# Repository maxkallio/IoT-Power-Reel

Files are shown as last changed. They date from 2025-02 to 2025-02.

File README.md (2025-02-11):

## Introduction

`IoT - Power` is a system for lending power reels in the HBO-ICT faculty on campus.

Students can use this system with their student cards to authenticate to the server, so that they can retrieve a power reel.

## Development

This project consists of two major components, found in their respective directories.

- Embedded
- Web

These two components work together to form the system as a whole.

### Embedded

The embedded directory contains all code for the microcontroller. IoT - Power uses <a href="https://platformio.org/">PlatformIO</a>, a framework for embedded systems for embedded code.

### Web

The web component consits of a database (SQL, MariaDB) and a LEMP stack.

### Running IoT - Power

Both components have to be deployed for this project to work.

#### Web
```shell
docker-compose -f docker-compose-test.yml up -d --force-recreate --build
```

#### Embedded

For the embedded system you first need to change the config to point to the deployed webserver. Then use PlatformIO to compile and upload the code to your microcontroller.
There's two different deployment modes. For each deployment mode different firmware is built. With platformIO you can choose between:
- Offline mode
- Online mode

Refer to the platformio.ini to find the differences between the two. There's some additional configuration needed for each mode however.

##### Online mode

In the platformio.ini you need to change the `BASE_URL` param to the IP address of the backend server.

e.g. `\"http://145.92.189.162/api/\"`. Please note the escape backticks in this `BASE_URL` param, this is mandatory!

##### Offline mode

In `/embedded/src/locker-offline.cpp` the inititlization of a struct `locker` named `lockers` can be found. This struct is a mapping of locking pins to the lockers along it's current state. In it's header file you can find it's definition.

You need to change `lockers` to the amount of lockers used in the deployment, with a correct mapping of locking pins to the locker.# IoT-Power-Reel
# IoT-Power-Reel
# IoT-Power-Reel

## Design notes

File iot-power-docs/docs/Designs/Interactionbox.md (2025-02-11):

# Interaction Box Design

## The board

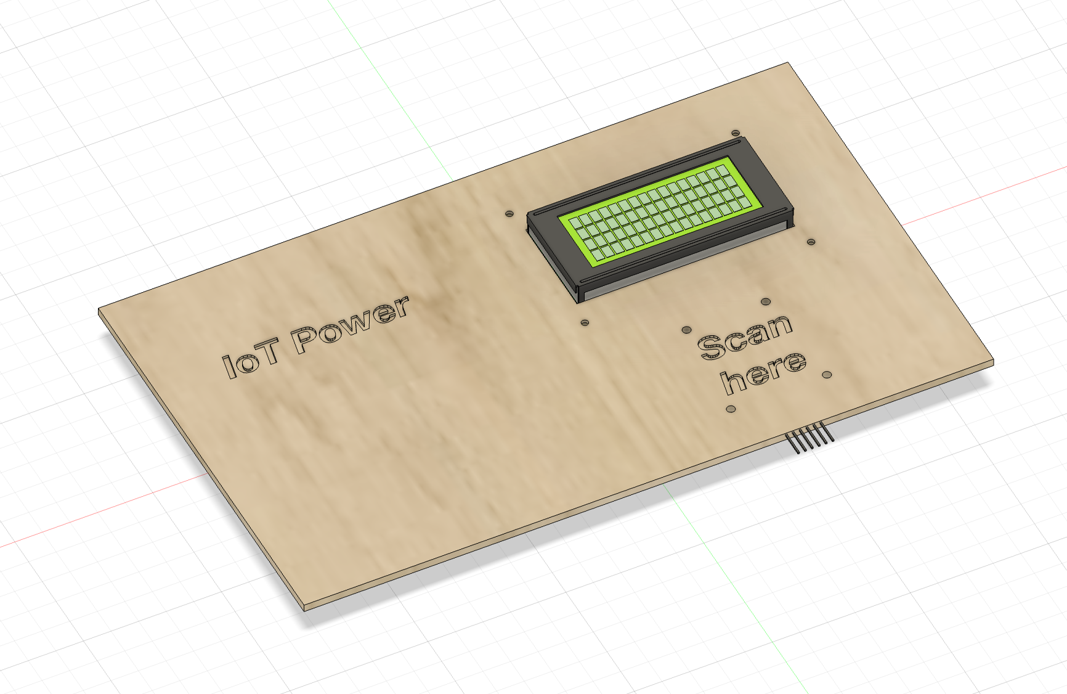
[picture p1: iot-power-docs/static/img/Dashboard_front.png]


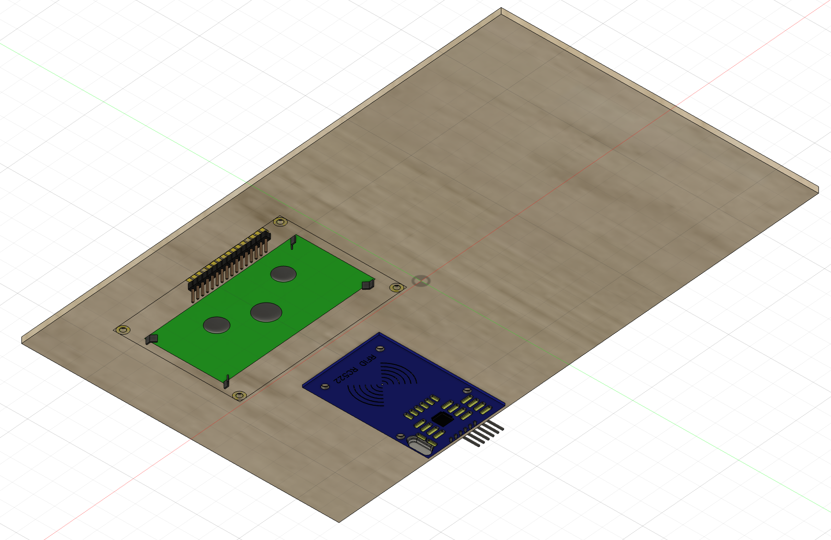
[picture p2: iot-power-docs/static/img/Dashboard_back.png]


### Overview
This is a main board to hold essential components for the device. It is crafted to  mount a 16x4 LCD screen and an RC522 RFID scanner module. The board will be fabricated using a laser cutter and 3mm plywood.

"IoT Power" is engraved on the left side of the board and "Scan here" is engraved near the RFID scanner to indicate its purpose.

### Material specifications
- 3mm plywood  
- The board dimensions are 250mm x 150mm

### Notes
- The engraved labels will guide users to understand the functionality of each component.
- The plywood material gives an eco-friendly aesthetic, while being sturdy enough to hold the components securely.

### Files

- [Fusion 360 file](https://gitlab.fdmci.hva.nl/IoT/2024-2025-semester-1/group-project/yoogaaciinuu24/-/blob/main/design/Dashboard.f3z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)
- [STL file (preview on GitLab available)](https://gitlab.fdmci.hva.nl/IoT/2024-2025-semester-1/group-project/yoogaaciinuu24/-/blob/main/design/Dashboard.stl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)
- [DXF file for laser cutting](https://gitlab.fdmci.hva.nl/IoT/2024-2025-semester-1/group-project/yoogaaciinuu24/-/blob/main/design/Dashboard_with_engraving.dxf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)

### Update

This board was updated and transformed into a box to hold more embedded components such as the breadboard and the microcontroller

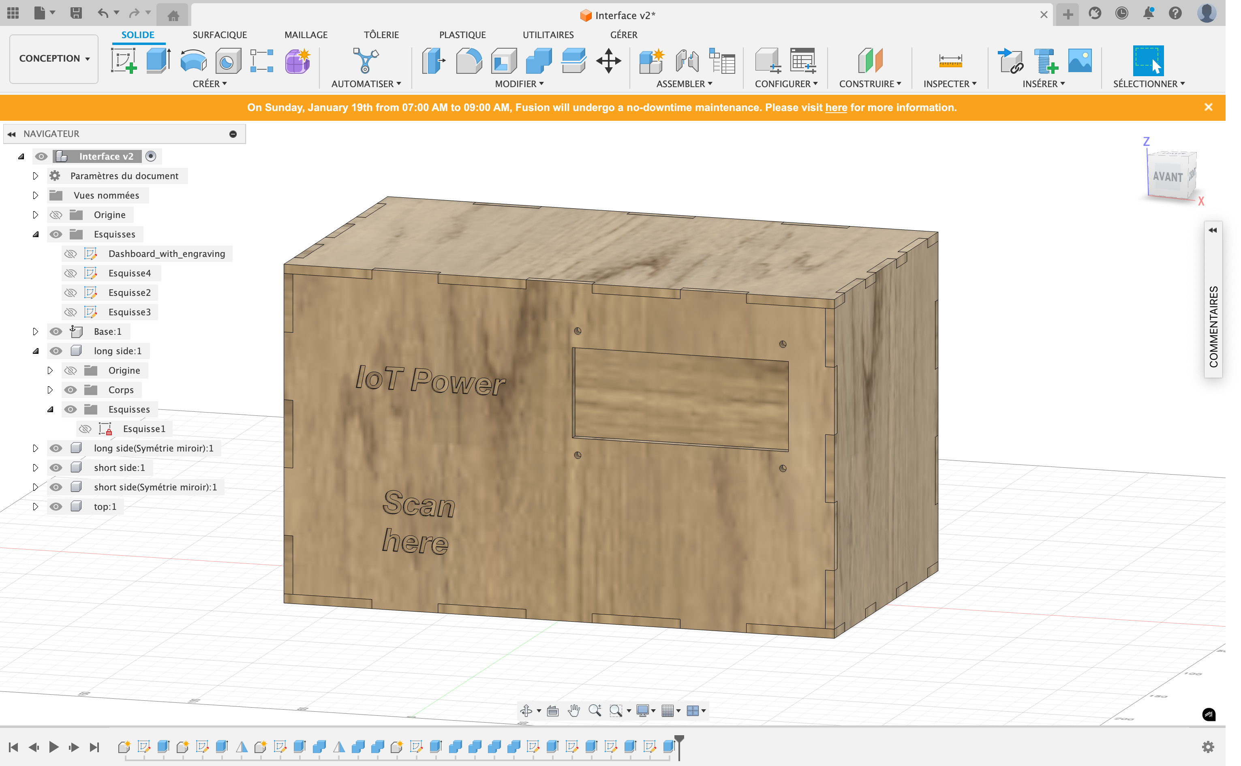
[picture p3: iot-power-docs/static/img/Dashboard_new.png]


## The locker

## Overview

The second version of the locker prototype improves upon the initial design by incorporating finger joints for increased durability and ease of assembly. This version also includes stackable features and additional support to align with the project's requirements for modularity and robustness.

---

## Key Features

- **Finger joints for durability**
   - Finger joints were designed in Fusion 360 to improve the structural integrity of the locker.
   - The joints allow precise interlocking of panels, reducing the reliance on adhesives.
   - A tutorial was followed to implement these joints effectively ([Fusion 360 Finger Joints Tutorial](https://www.youtube.com/watch?v=ZrcqauNvt0M)).

- **Two 4mm wood sheets**
   - The prototype uses 4mm-thick MDF wood sheets, chosen for their affordability and ease of laser cutting.
   - Edges are reinforced with finger joints to ensure durability under repeated stacking or handling.

- **Stackable edges**
   - The top and bottom edges of the locker were modified to include alignment guides, allowing multiple lockers to be securely stacked.
   - This feature adds modularity and flexibility for applications requiring expandable storage systems.

- **Adjustments with AutoCAD**
   - After initial design in Fusion 360, minor adjustments were made in AutoCAD adjust the dimensions.
   - The adjustments focused on tolerances to account for the laser cutter's kerf and material thickness.

---

## Manufacturing process

1. **Design**
   - Created the overall shape and added finger joints in Fusion 360.
   - Ensured all edges aligned perfectly for clean assembly.
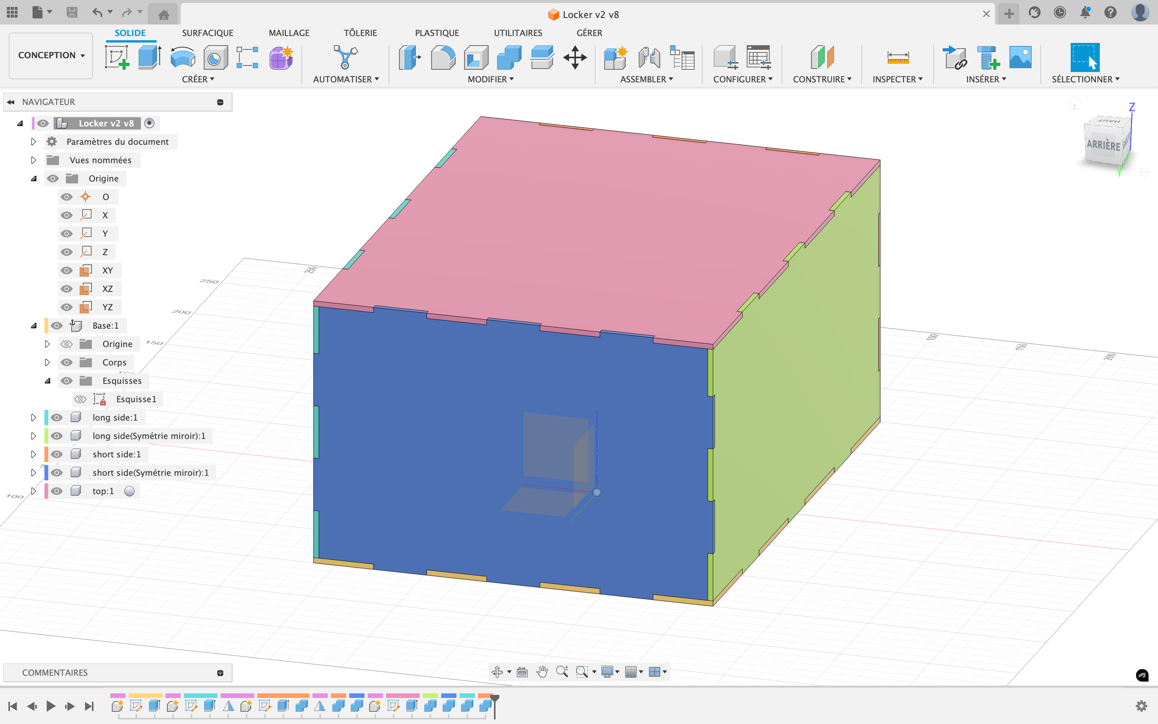
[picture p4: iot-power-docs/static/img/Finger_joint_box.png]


2. **Adjustment**
   - Exported the design to AutoCAD for precise dimensional adjustments.
   - Verified tolerances for the laser cutter.
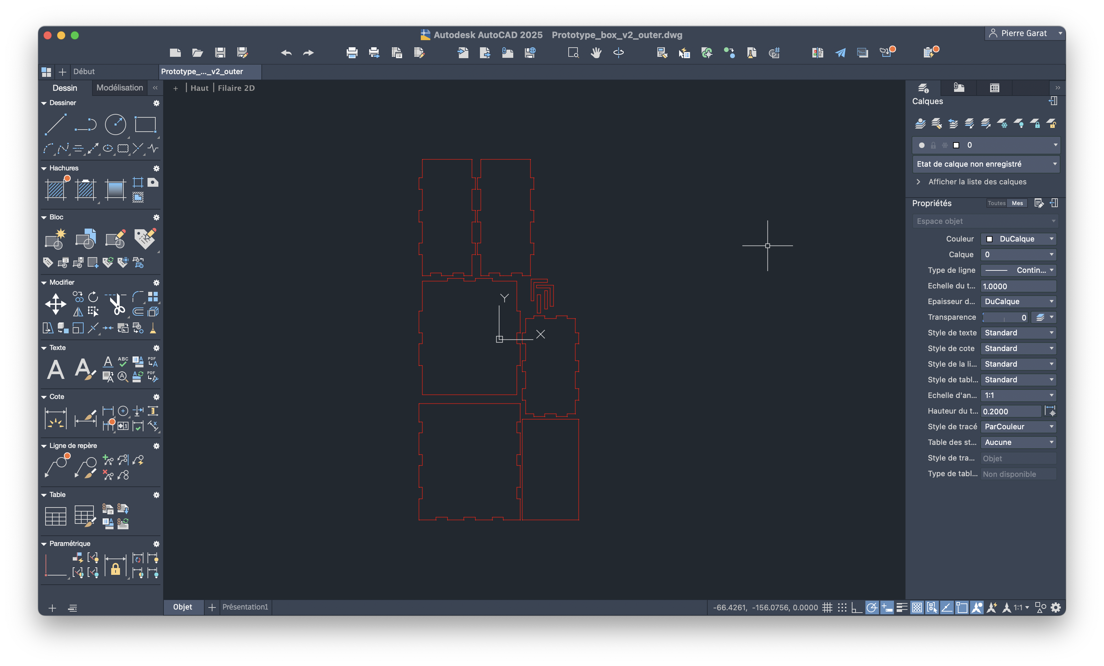
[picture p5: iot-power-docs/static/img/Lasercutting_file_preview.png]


3. **Fabrication**
   - Laser-cut all panels from two 4mm MDF sheets.
   - Assembled the panels manually, interlocking the finger joints.
   - Tested stacking alignment and structural integrity.

## Files

- [Fusion 360 file](https://gitlab.fdmci.hva.nl/IoT/2024-2025-semester-1/group-project/yoogaaciinuu24/-/blob/main/design/Locker_v2.f3d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)
- [STL file (preview on GitLab available)](https://gitlab.fdmci.hva.nl/IoT/2024-2025-semester-1/group-project/yoogaaciinuu24/-/blob/main/design/Locker_v2.dxf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)
- [DXF file for laser cutting](https://gitlab.fdmci.hva.nl/IoT/2024-2025-semester-1/group-project/yoogaaciinuu24/-/blob/main/design/Prototype_box_v2.dxf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)
- [DXF outer file for laser cutting](https://gitlab.fdmci.hva.nl/IoT/2024-2025-semester-1/group-project/yoogaaciinuu24/-/blob/main/design/Prototype_box_v2_outer.dxf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)

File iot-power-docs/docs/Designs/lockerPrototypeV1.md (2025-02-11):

# First prototype of the locker

The first prototype was created using Fusion 360. This tool makes it possible to create 3D designs that can be used in the makers lab. By exporting the sketch made in the tool the laser cutter can be used. To explain the way of making the design I have created this documentation file. After explaining the prototype I will discuss the improvements that have to made in the second prototype. The following topics will be discussed in this file.

1. The design
2. Laser cutting
3. The materials
4. Improvements for the next prototype

## The design

As mentioned before Fusion 360 was used in the design of the first prototype. Below is an image of the design with numbers of parts that are explained below. The Fusion 360 file is also added to the project in the static/design folder named LockerDesignV1.

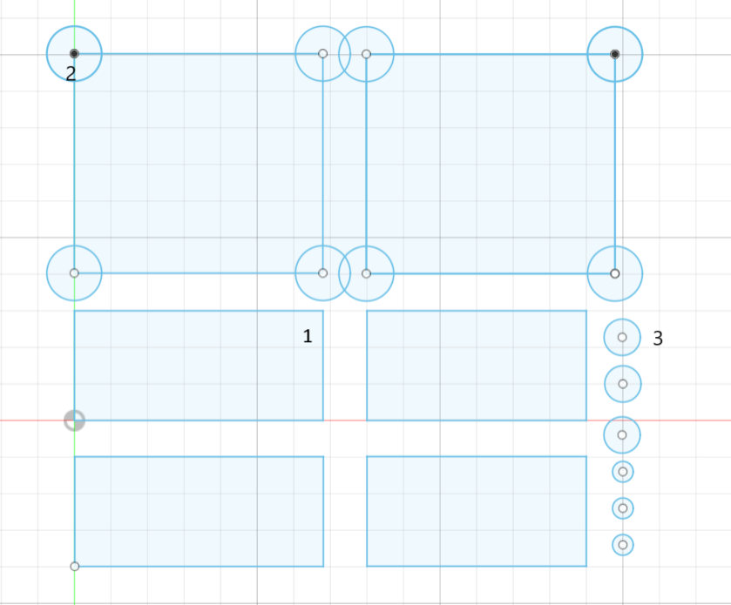
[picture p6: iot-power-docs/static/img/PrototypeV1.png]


1. These are the wall of the locker. There are two shorter back wall and two longer side walls. The dimensions used are based on power cable dimesnions found on the internet. I found multiple dimensions so to be sure the power cable would fit I used the biggest dimensions found.

2. These are the top and bottom parts of the locker. The cicles in the corners are used to make the indentations in the plywood. After uploading the sketch to the laser cutting program I removed the part of the circle that exceeds the boundaries of the rectangle. Only the ceeling of the locker should have a indentation but I used the indentation marks of the wall to make raised cutouts to attatch to the floor of the locker. This was done by moving the new quarter circles to the side of the box and cutting these out separately.

3. These circles are used to make the doorknob of the locker. By having multiple smaller and at least one bigger circle the circles can be glued together. This makes for a cone with a bigger end. This is turn results in a doorknob.

## Laser cutting

After making the design the next step of the prototype was using the laser cutter in the Makerslab. This was done by uploading the sketch to a USB and loading it into the computers used for laser cutting. I gave the lines that should be indented a red color and the lines that should be cut a black line. By setting different laser depts in the settings of the tool used by the computer I was able to make a differentiation in cutting and engraving. I baught the thickest plywood available and set the cutting settings accordingly. By weighing the plywood down at the edges I was able to compensate a slight curve in the wood.

After using the buttons on the laser cutter I found that the design of the locker was to big for the plywood. This resulted in me having to cut the desing in half and cutting two separate pieces of plywood. This was no big issue because I could use the design tool of the computer attatched to the laser cutter to do this. After cutting two pieces of plywood I now had the plywood parts to assamble the locker. I did not have all the materials yet because I needed bolts, nuts and a doorhinge. I taught that I could get these parts from the Makerslab but only the correct bolts were present. This resulted in me having to go to Praxis to get the right parts. The walls, ceeling and floor were glued together and the bolts were screwed into the wood using a screwdriver. By gluing the circels together I created the doorknob. I also glued the raised corners to the floor of the locker this was the last part to add.

After all these steps the locker was assembled. The images below shows the locker after it was finished.

### Locker top view
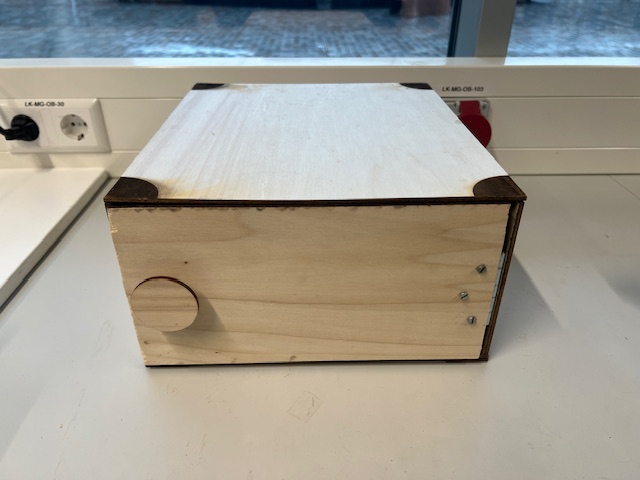
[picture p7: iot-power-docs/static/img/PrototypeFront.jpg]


### Locker top view with open door
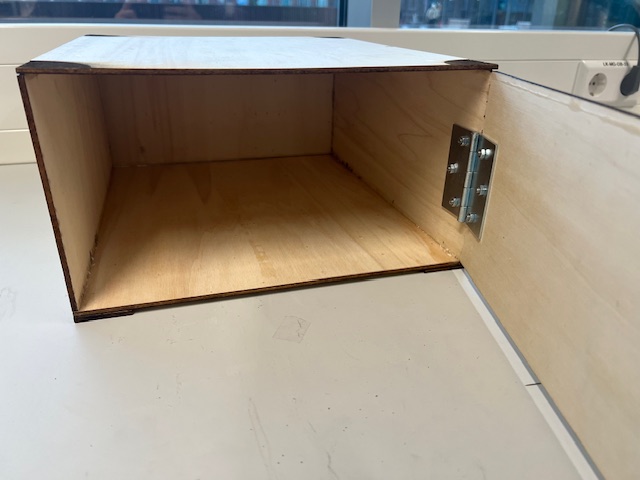
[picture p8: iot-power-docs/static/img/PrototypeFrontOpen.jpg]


### Locker bottom view
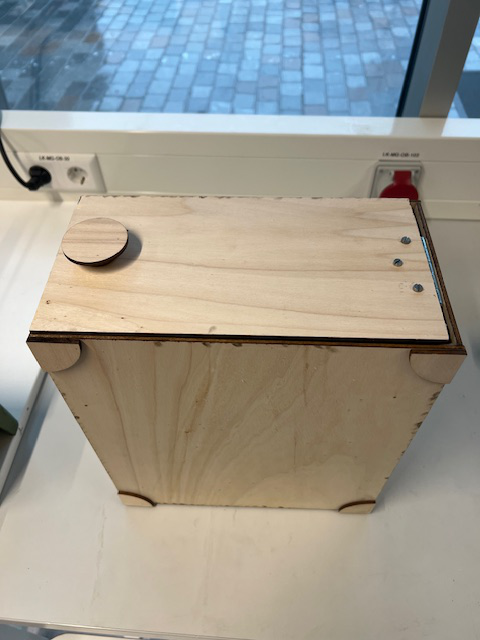
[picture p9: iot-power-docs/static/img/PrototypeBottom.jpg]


## The materials
There are multiple materials used for the locker. The most important part is the plywood used. we asked the Makerslab for the strongest wood they had and they advised me to use MDF wood. This plywood is still not very strong or thick but if we want to use stronger wood we have to decide on using wood baught from a hardware store.

As mentioned before the makerslab only had bolts that could be used in assembling the locker. The Makerslab had nuts but not the correct size for the hinge we were using. The hinge itself had to be baught from Praxis because the Makerslab nad no hinges available. 

The hinge baught was a 70x70mm doorhinge of the brand I-Fix. The nuts used have a size called M4 and are described as zeskantmour gegalviniseerd. The producer of the nuts is called Maxeda DIY. The bolts used for the locker were available in the makerslab and were the smallets bolts available. These were the only bolts to fit the holes in the doorhinges.

## Improvements for the next prototype
After building the prototype we found that the wood used in the desing was not very sturdy. The wood used should be altered becasue the locker is not very strong and the walls can be broken easily. To get better wood for the next prototype we need to go to a hardware store and buy stronger wood. The desing also does not offer an easy was to attatch the sides of the locker together. The sides have to be glued and only the glue is holding the locker together. This could become a problem when multiple lockers are stacked on top of eachother. By using a interlocking desing called a finger desing the walls fit together better and the locker should be stronger. This idea came from the drawer test that was printed to test the settings and desings made for laser cutting.

The indents of the locker are not very deep because the plywood used is very thin. This results in the locker possibly not fitting on top of eachother very good. By using thicker wood the indentations made can be made deeper and the lockers should not be movable by pusing or pulling an individual locker.

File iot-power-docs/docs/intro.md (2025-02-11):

# IoT Power - Intro

## Overview

**IoT Power** is a solution to address the shortage of power outlets in HvA's educational facilities by creating a secure and automated system for lending power reels. The system allows students to borrow and return power cable reels by scanning their HvA ID cards.

---

## Assignment Details

### Cause
With an increasing number of students and digital devices, HvA faces a shortage of power outlets. The current solution—lending power cable reels—suffers from inefficiencies as reels are often not returned. IoT Power aims to solve this issue by automating the lending and tracking process.

### Goal
Building an installation and infrastructure that enables secure and efficient lending of power reels.

---

## Features

1. **RFID-based authentication**
  - Students identify themselves by scanning their HvA ID cards.

2. **Borrow and return management**
  - The system logs which student has checked out or returned a reel.

3. **Centralized dashboard**
  - An administrative dashboard for tracking overdue reels and managing inventory.

4. **Wireless Connections**
  - All interactions between the shelf and the reels are conducted wirelessly.

---

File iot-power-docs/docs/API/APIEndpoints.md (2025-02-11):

# API documentation
Details of the endpoints, their purpose, parameters, and responses.

---

#### Base URL
```
http://<server>/api/get.php
```

---

### Endpoints

#### **Get available locker**
- **URL**: `/getAvailableLocker`
- **Method**: `GET`
- **Description**: Retrieves a locker number for an available locker.
- **Parameters**: None
- **Response**:
  - **Success**:
    ```json
    {
        "success": true,
        "locker_number": <locker_number>
    }
    ```
  - **Failure**:
    ```json
    {
        "success": false,
        "locker_number": "No locker found."
    }
    ```

---

#### **Get available cable**
- **URL**: `/getAvailableCable`
- **Method**: `GET`
- **Description**: Retrieves a cable ID for an available cable.
- **Parameters**: None
- **Response**:
  - **Success**:
    ```json
    {
        "cable_id": <cable_id>
    }
    ```
  - **Failure**:
    ```json
    {
        "cable_id": "No cable found."
    }
    ```

---

#### **Get all cables**
- **URL**: `/getCables`
- **Method**: `GET`
- **Description**: Fetches all cables from the database.
- **Parameters**: None
- **Response**:
  - **Success**:
    ```json
    {
        "success": true,
        "data": [
            {
                "cable_id": <cable_id>,
                "cable_status": <status>,
                "user_id": <user_id>,
                "check_in": <check_in_date>,
                "check_out": <check_out_date>
            },
            ...
        ]
    }
    ```
  - **Failure**:
    ```json
    {
        "success": false,
        "data": "No results"
    }
    ```

---

#### **Get user details**
- **URL**: `/getUser?parameters:<user_id>`
- **Method**: `GET`
- **Description**: Fetches user details based on the given `user_id`.
- **Parameters**:
  - **`parameters`**: The user ID to fetch details for.
- **Response**:
  - **Success**:
    ```json
    {
        "success": true,
        "data": [
            {
                "user_id": <user_id>,
                "name": <user_name>,
                ...
            }
        ]
    }
    ```
  - **Failure**:
    ```json
    {
        "success": false,
        "data": "No results"
    }
    ```

---

#### **Scanned card**
- **URL**: `/scannedCard`
- **Method**: `POST`
- **Description**: Handles user actions when scanning their card. If the user has a cable, it will return it. Otherwise, it assigns a free cable to the user.
- **Parameters**:
  - **`user_id`**: The ID of the user scanning their card.
- **Response**:
  - **If the user returns a cable**:
    ```json
    {
        "success": true,
        "message": "Cable returned successfully."
    }
    ```
  - **If the user is assigned a cable**:
    ```json
    {
        "success": true,
        "message": "Cable assigned successfully."
    }
    ```
  - **If no free cables are available**:
    ```json
    {
        "success": false,
        "message": "No cables available."
    }
    ```
  - **If the `user_id` parameter is missing**:
    ```json
    {
        "success": false,
        "message": "Missing user_id parameter."
    }
    ```
  - **If there is an error returning a cable**:
    ```json
    {
        "success": false,
        "message": "Failed to return cable."
    }
    ```
  - **If there is an error assigning a cable**:
    ```json
    {
        "success": false,
        "message": "Failed to assign cable."
    }
    ```

---

### **Setup and usage notes**
- **Database connection**: The API relies on a global `$dbConnection` object for database interactions.
- **Error handling**: Each function provides clear success or failure messages in JSON format.
- **URL parsing**: The `$_SERVER['REQUEST_URI']` is used to determine the function to call based on the endpoint name.

---

### **Example Usage**

#### Fetch an Available Locker
**Request**:
```
GET /getAvailableLocker
```
**Response**:
```json
{
    "success": true,
    "locker_number": 5
}
```

---

#### Assign or return a cable
**Request**:
```
POST /scannedCard
Content-Type: application/json

{
    "user_id": "12345"
}
```
**Response** (User assigned a cable):
```json
{
    "success": true,
    "message": "Cable assigned successfully."
}
```

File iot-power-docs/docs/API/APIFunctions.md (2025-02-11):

# Back-end API Functions

In this documentation page all the API code is explained. Our API consists of a CRUD operation that is made in the web folder of the project. By using Docker the api folder of the web part of the project is created as a back-end API of the IoT Power website. This page goes into all the functionalities that are created in the api folder. The API is used to make queries to the database of our project. Some queries are complex and do not fit into one of the CRUD operations. This resulted in some functions having different kind of CRUD operations in the CRUD named file they are in. This should not really matter because the main objective of the operation determence the placing in a file.

To understand our API it is important to first separate the files between different CRUD operations. The CRUD approach that we are using results in the following php files:

1. get.php
2. update.php

To connect to the database a db.php file is also created.

Every php file has the same top part that makes it possible to call funtions from a url in our project. For example typing http://localhost/api/get.php?getUser?parameters:1 in Chrome will restult in a Json object that contains the user with ID 1. The functionality that is added to every php file except for the db.php file is the following code.

```php
    // Get the url and select the part after the question mark to know what function to call.
    $url = $_SERVER['REQUEST_URI'];
    $url = str_replace("/api/get.php?", "", $url);

    // Check if url contains parameters.
    if(str_contains($url, "?parameters:") == true) {
        $url = substr($url, 0, strpos($url, "?parameters:"));
    }
```

The code snippet below results in an variable where the function name is separated from the url. The functionality also makes sure the api call includes the correct file name to look at the functions in this file. For this url the functionality looks for get.php being added to the url to make sure the code is trying to reach the get.php file.

After doing this the url variable can be used to call functions in the get.php file. This is done by having multiple if statements that check for function names. The code snippet below shows two of these if statements.

```php
    // Call the correct function from the given url when the parameters are removed.
    if ($url == "getAvailableLocker"){
        getAvailableLocker();
    }
    if ($url == "getAvailableCable"){
        getAvailableCable();
    }
```

## db.php
The db.php file is an simple file to crate a database connection. This is done using a msqli function that creates a new database connection. This database connection can be used in the entire project by including db.php in other php files.

```php
    // Main file for connecting to the database as instructed on the back end page of the knowledgebase.
    $dbConnection = new mysqli("mariadb", "root", "root123", "locker");

    if ($dbConnection->connect_error) {
        echo json_encode(array("success" => false, "error" => $dbConnection->connect_error));
        exit();
    }
```

## get.php
The get.php file is used to get data from the database. The file has the following functions:

* getAvailableLocker
* getAvailableCable
* getCables
* getUser
* getTransactions
* getOverdueTransactions

The getAvailableLocker function gets a locker from the database that has a status of Free. The function only wants one locker to be returned by the database and this is why the query shown below uses a LIMIT clause. The code below does a query request to the database and now gets a result from the query. To check if the query has succeded the number of rows that are returned should be bigger than 0.

```php
    // Get a locker number for an available locker.
    function getAvailableLocker() {
        global $dbConnection;
        // Query for fetching the rolls.
        $sql = "SELECT locker_number FROM Locker l WHERE l.locker_status = 'Free' LIMIT 1";
        $result = $dbConnection->query($sql);
        $row = $result -> fetch_assoc();

        if ($result->num_rows > 0) {
            echo json_encode(array("success" => true, "locker_number" => $row["locker_number"]));
        } else {
            echo json_encode(array("success" => false, "locker_number" => "No locker found."));
        }
    }
```

The getAvailableCable function gets a cable from the database that has a status of Free. The function only wants one cable to be returned by the database and this is why the query shown below uses a LIMIT clause. The code below does a query request to the database and now gets a result from the query. To check if the query has succeded the number of rows that are returned should be bigger than 0.

```php
    // Get a cable number for an available cable.
    function getAvailableCable() {
        global $dbConnection;
        // Query for fetching the rolls.
        $sql = "SELECT cable_id FROM Cable c WHERE c.cable_status = 'Free' LIMIT 1";
        $result = $dbConnection->query($sql);

        if ($result->num_rows > 0) {
            echo json_encode($result->fetch_assoc());
        } else {
            echo json_encode(array("cable_id" => "No cable found."));
        }
    }
```

The getCables function gets all cables from the database. This is easily done by selecting all columns from the cable table without setting a WHERE clause. The query succeeds when more than 0 rows are returned, because the database will always have cables. This means that when at least one cable is returned the query has succeeded. This database query is used in the cable dashboard of our IoT Power website. The dashboard needs all cables to make a HTML table that shows the cables.

```php
    function getCables() {
        global $dbConnection;
        // Query for fetching the cables.
        $sql = "SELECT * FROM Cable";
        $result = $dbConnection->query($sql);

        if ($result->num_rows > 0) {
            while($row = $result->fetch_assoc()) {
                $data[] = $row;
            }
            echo json_encode(array("success" => true, "data" => $data));
        } else {
            echo json_encode(array("success" => false, "data" => "No results"));
        }
    }
```

The getUser function is used to get a specific user from the user table. This is needed because the cable and transaction tables only store a user id. To display a name in our dashboards the user name has to be retrieved by using the user id. This can by done with the parameters of the getUser request. The code will set parameters in the url API query made in the front-end.

First the getUser function has to separate the parameters from the url. This is done by using the standard way the url is made up. The part of the url after parameters: contains the parameters. Now that the parameters are known a simple database query can be made to get the correct user from the database.

```php
    function getUser() {
        global $dbConnection;
        // Get the parameters from the URL.
        $parameters = $_SERVER['REQUEST_URI'];
        $parameters = substr($parameters, strpos($parameters, "?parameters:") + 1);
        $parameters = str_replace("parameters:", "", $parameters);
        // Query for fetching a user.
        $sql = $dbConnection->prepare("SELECT * FROM User u WHERE u.user_id = ?");
        $sql->bind_param("s", $parameters);
        $sql->execute();
        $result = $sql->get_result();

        if ($result->num_rows > 0) {
            while($row = $result->fetch_assoc()) {
                $data[] = $row;
            }
            echo json_encode(array("success" => true, "data" => $data));
        } else {
            echo json_encode(array("success" => false, "data" => "No results"));
        }
    }
```

The getTransactions function gets all transactions from the database. This is needed for the transactions dashboard in the front-end. The function looks like the get cabless function and acts in the same way. The only difference is the fact that the transactions are retrieved instead of the cables.

```php
    function getTransactions() {
        global $dbConnection;
        // Query for fetching the transactions.
        $sql = "SELECT * FROM Transaction";
        $result = $dbConnection->query($sql);

        if ($result->num_rows > 0) {
            while($row = $result->fetch_assoc()) {
                $data[] = $row;
            }
            echo json_encode(array("success" => true, "data" => $data));
        } else {
            echo json_encode(array("success" => false, "data" => "No results"));
        }
    }
```

The getOverdueTransactions function gets all transactions that are overdue from the database. This can be done by setting the WHERE clause of the query. The clause should check the transactions table for transactions that have a check_out data that is more than one day ago. This makes a transaction overdue. This is because the transactions that are made more than one day ago and were not returned the same day include missing cables. The query should also include the fact that a transaction with a check_in value is a transaction that is completed. The WHERE clause should include two restrictions becuase of this. t.check_out < (CURDATE() - INTERVAL 1 DAY) to check that a transaction is later than a day and t.check_in IS NULL to check if a transaction was not completed.

```php
    function getOverdueTransactions(){
        global $dbConnection;
        // Query for fetching the transactions.
        $sql = "SELECT * FROM Transaction t WHERE t.check_out < (CURDATE() - INTERVAL 1 DAY) AND t.check_in IS NULL";
        $result = $dbConnection->query($sql);

        if ($result->num_rows > 0) {
            while($row = $result->fetch_assoc()) {
                $data[] = $row;
            }
            echo json_encode(array("success" => true, "data" => $data));
        } else {
            echo json_encode(array("success" => false, "data" => "No results"));
        }
    }
```

## update.php
The update.php file is used to change data in the database. Some of the queries used in the file are different CRUD operations but the main goal of the functions are to achieve a change in the databse. The functions in the update.php file are.

* setStatusLocker
* setStatusCable
* setStatusForLending
* transactionBasedStatusUpdate

The setStatusLocker, setStatusCable, setStatusForLending functions where created before there was one function to execute all of these functionalities. Thes functions are not really used in our project any more. This is the reason that only the transactionBasedStatusUpdate will be explained on this page.

The transactionBasedStatusUpdate function can be separated into two parts. This is because the function starts by checking what kind of interaction the user is doing with the locker. This function is used when a user scans a card on the IoT Power station and tries to unlock a locker to either retrieve or return a cable. The function will know what kind of interaction the user is trying to do because of the transaction table in the database. When a user has a transaction in the transaction table that has no check_in the user is trying to check_in a cable. This means that all transaction without a check_in DATETIME are pending transactions or transactions that include cables that are lend out. By using this information in the query of the function a separation can be made between returning and lending cables.

```php
    // Function that updates the cable and locker status based on the transaction attatched to the user.
    global $dbConnection;
    // Get the parameters from the URL.
    $parameters = $_SERVER['REQUEST_URI'];
    $parameters = substr($parameters, strpos($parameters, "?parameters:") + 1);
    $parameters = str_replace("parameters:", "", $parameters);
    // Query for getting a pending transaction for the given user
    $sql = $dbConnection->prepare("SELECT * FROM transaction t WHERE t.user_id = ? AND t.check_in IS NULL");
    $sql->bind_param("s", $parameters);
    $sql->execute();
    $transaction = $sql->get_result();
```

A lot of the queries in the transactionBasedStatusUpdate function use the parameter send to the function in the url. The parameters send is the user id read from the RFID card that is scanned on the IoT Power station.

The part of the transactionBasedStatusUpdate function that handels a user returning a reel is desribed in the code snippet below. If the query above resulted in a transaction being found the user still has a cable and wants to return a power reel. Now that it is known that a user is returning a power cable the function will try to find an available locker for the user to put the cable in. This is done in the first query. When and if a locker is found a couple of mutation on the database can be done. The Locker that is assigned to the return of the cable should now have status taken because this locker will be used to store the cable. If the mutation works the cable that the user is retruning should be altered in the database. The locker_id, cable_status and user_id should be changed becuase all these values change after the return is completed. The cable now has a locker it is stored in, has status free and has no current user any more. Now the transaction that include a rented cable should be closed by setting the check_in date to the current time and date. This is done using the user id sent to the function in the parameters.

After all these values are updated the function should return the locker where the user can store their cable in. This is done because the embedded device should display the locker that is used for the retrun to the user using the LCD screen.

```php
    // Check if there is a transaction pending for the user the interaction is returning a reel.
    if ($transaction->num_rows > 0) {
        // Query for fetching an available locker.
        $sql = "SELECT locker_id FROM Locker l WHERE l.locker_status = 'Free' LIMIT 1";
        $result = $dbConnection->query($sql);
        $row1 = $result -> fetch_assoc();
        $lockerId = $row1["locker_id"];
        // If there is an available locker use the locker to alter values in the cable and locker tables.
        if ($result->num_rows > 0) {
            // Query to set the status of the locker with the found ID.
            $sql = $dbConnection->prepare("UPDATE Locker SET locker_status = 'Taken' WHERE locker_id = ?");
            $sql->bind_param("s", $lockerId);
            $sql->execute();
            // Return if the insert was successful or not.
            if ($sql->affected_rows > 0) {
                // The cable does now have a locker where it is stored in so the locker id should be set to the correct id.
                // Query to set the locker id in the cable table.
                $sql = $dbConnection->prepare("UPDATE Cable SET locker_id = ? WHERE user_id = ?");
                $sql->bind_param("ss", $lockerId, $parameters);
                $sql->execute();
                // Query to set the status in the cable table.
                $sql = $dbConnection->prepare("UPDATE Cable SET cable_status = 'Free' WHERE user_id = ?");
                $sql->bind_param("s", $parameters);
                $sql->execute();
                // Query to set the user in the cable table.
                $sql = $dbConnection->prepare("UPDATE Cable SET user_id = NULL WHERE user_id = ?");
                $sql->bind_param("s", $parameters);
                $sql->execute();
                // Query to set the transaction in the transaction table.
                $sql = $dbConnection->prepare("UPDATE Transaction SET check_in = NOW() WHERE user_id = ?");
                $sql->bind_param("s", $parameters);
                $sql->execute();
                // Return if the insert was successful or not.
                if ($sql->affected_rows > 0) {
                    // Last step is to echo the locker that is available for the user to return the power reel to.
                    // Query for fetching an available locker.
                    $sql = $dbConnection->prepare("SELECT locker_number FROM Locker l WHERE l.locker_id = ?");
                    $sql->bind_param("s", $lockerId);
                    $sql->execute();
                    $result = $sql->get_result();
                    $row2 = $result -> fetch_assoc();
                    echo json_encode(array("success" => true, "locker_number" => $row2["locker_number"]));
                } else {
                    echo json_encode(array("success" => false, "locker_number" => "No locker found.", "Else place" => "3th returning"));
                }            
            } else {
                echo json_encode(array("success" => false, "locker_number" => "No locker found.", "Else place" => "2nd returning"));
            }        
        } else {
            echo json_encode(array("success" => false, "locker_number" => "No locker found.", "Else place" => "1st returning"));
        }
    }

```

If the transactionBasedStatusUpdate function concludes that the user is renting a cable becuase the user has no open transactions the code snippet below is run. The function will first select a locker that is taken and therefor has a cable inside of it. After a locker is found that contains a cable a couple of mutations have to be made to the database. First the cable id has to be found that is attatched to the locker that is being opened. This is used because after this the locker will be empty and the correct cable can not be found any more using a locker id. Now that the cable id is safely stored the cable id can lose the stored locker id because the cable is not stored in a locker any more. The status of the locker and cable will also change. The user id of the user now renting the cable will be stored in the cable id because the cable is now attatched to a user instead of a locker.

After changing both the locker and cable tables in the database the function will create a new transaction. All values of the transaction will be set except of the check_in value. This is becasue this value can only be set when returning a cable to the locker station.

The last step of the function is again returning the locker that is being used to retrieve a cable. This is done because the embedded device should display the locker that is opened for the user to rend a cable using the LCD screen.

```php
    // If there is no transaction pending for the user the interaction is lending a reel. 
    else {
        // Query for fetching a taken locker.
        $sql = "SELECT locker_id FROM Locker l WHERE l.locker_status = 'Taken' LIMIT 1";
        $result = $dbConnection->query($sql);
        $row1 = $result -> fetch_assoc();
        $lockerId = $row1["locker_id"];
        if ($result->num_rows > 0) {
            // Query for fetching the cable id.
            $sql = $dbConnection->prepare("SELECT cable_id FROM Cable c WHERE c.locker_id = ?");
            $sql->bind_param("s", $lockerId);
            $sql->execute();
            $result = $sql->get_result();
            $row2 = $result -> fetch_assoc();
            $cableId = $row2["cable_id"];
            // Query to set the status of the locker with the found ID.
            $sql = $dbConnection->prepare("UPDATE Locker SET locker_status = 'Free' WHERE locker_id = ?");
            $sql->bind_param("s", $lockerId);
            $sql->execute();
            // Query to set the status of the cable.
            $sql = $dbConnection->prepare("UPDATE Cable SET cable_status = 'Taken' WHERE locker_id = ?");
            $sql->bind_param("s", $lockerId);
            $sql->execute();
            // Query to set the user of the cable.
            $sql = $dbConnection->prepare("UPDATE Cable SET user_id = ? WHERE locker_id = ?");
            $sql->bind_param("ss", $parameters, $lockerId);
            $sql->execute();
            // Query to set the locker id of the cable.
            $sql = $dbConnection->prepare("UPDATE Cable SET locker_id = NULL WHERE locker_id = ?");
            $sql->bind_param("s", $lockerId);
            $sql->execute();
            echo $sql->affected_rows;
            echo $sql->affected_rows > 0;
            // Return if the insert was successful or not.
            if ($sql->affected_rows > 0) {
                // Query to create a new transaction in the transaction table.
                // Set: check_out cable_id user_id
                $sql = $dbConnection->prepare("INSERT INTO transaction (check_out, cable_id, user_id) VALUES (NOW(), ?, ?)");
                $sql->bind_param("ss", $cableId, $parameters);
                $sql->execute();
                // Return if the insert was successful or not.
                if ($sql->affected_rows > 0) {
                    // Last step is to echo the locker that is available for the user to get a power reel from.
                    // Query for fetching an available locker.
                    $sql = $dbConnection->prepare("SELECT locker_number FROM Locker l WHERE l.locker_id = ?");
                    $sql->bind_param("s", $lockerId);
                    $sql->execute();
                    $result = $sql->get_result();
                    $row3 = $result -> fetch_assoc();
                    echo json_encode(array("success" => true, "locker_number" => $row3["locker_number"]));
                } else {
                    echo json_encode(array("success" => false, "locker_number" => "No locker found.", "Else place" => "3th lending"));
                }
            } else {
                echo json_encode(array("success" => false, "locker_number" => "No locker found.", "Else place" => "2nd lending"));
            }        
        } else {
            echo json_encode(array("success" => false, "locker_number" => "No locker found.", "Else place" => "1st lending"));
        }
    }
```

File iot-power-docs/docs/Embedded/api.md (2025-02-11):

# API

To make API calls with our embedded device we created an api.cpp file that stores all fuctions that make API calls to our IoT Power back-end. The api calls work because of the wifi connection we esteblished in the connectivity.cpp file. The code explaination for this file can be found on the WiFi connection embedded documentation page.

The api.cpp file contains the following fucntions:

* getLockerNumber

## The getLockerNumber function

The getLockerNumber function gets an available locker from the back-end. This function on the back-end also changes the database to set the database fields for the changing locker and cable instances. The function on the API also creates or updates the transaction made. This means that by calling the getAvailableLocker function on the back-end all the mutations to the database are done. The locker that is returned is enough for the fucntionality of getting and setting a locker and cable. The only relevant variable that is retrieved from calling the url is the locker that is assigned to the user. The user can use the locker to store or retrieve a cable. The system knows the transaction type that is made because when a transaction has no delivery/check_in date the user has a cable and when there is no "pending" transaction for the user yet the user wants to get a new cable.

In the code snippet below it is visable that the function return the locker that is opened or the fact that no locker is found. When a API call is made the locker number is echod on the back-end in a Json object and can be retrieved by using httpClient.getString() and deserializeJson. Now the locker number stored in the Json object can be returned using jsonBuffer and the key that is set for the value which is locker_number.

```cpp
String getLockerNumber(){
  // Initialize a wi-fi client & http client.
  WiFiClient client;
  HTTPClient httpClient;

  // Do a GET request to the IoT Power api.
  String url = "http://145.92.189.162/api/get.php?getAvailableLocker";
  httpClient.begin(client, url);
  int httpCode = httpClient.GET();

  // Check if the response is fine.
  if(httpCode == HTTP_CODE_OK) { // HTTP_CODE_OK == 200
    // Print the body of the GET-request response.
    String payload = httpClient.getString();
    Serial.println(payload);
    deserializeJson(jsonBuffer, payload);
    return jsonBuffer["locker_number"];
  } else {
    Serial.println("Unable to connect :(");
    return "No locker found.";
  }
}
```

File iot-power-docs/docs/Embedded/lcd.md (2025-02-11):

# LCD
This is the documentation for the LCD screen on this page you can find a Fritzing diaram showing the wiring of the LCD screen to the Wemos D1 Mini. The page also has an explaination of the LCD code that makes the LCD scroll text in an idle state and makes the LCD show a unlocked message after a card is scanned.

## Wiring diagram
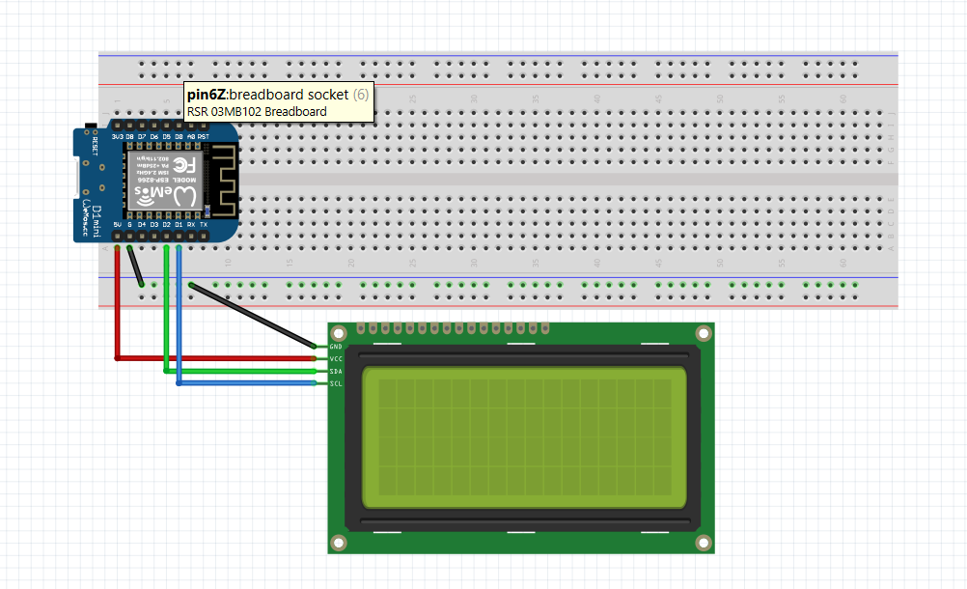
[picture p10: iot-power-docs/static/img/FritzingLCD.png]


## Code explainantion
The code that was made in PlatfromIo has two main functions. The LCDScroll and printLockerLCD functions. For both functions I will explain what happens in the functions.

### LCDScroll funtion
The LCDScroll function is the idle state for the LCD. The LCD shows a scrolling text when no interaction is made with the locker. This idle state happens beause the LCDScroll function is called every loop in the main.cpp file.

In the code snippet below you can see that the LCDScroll function keeps track of an index. This is used to keep track of how far the text on the LCD screen moved to the right. When the text would isappear from the screen the location of the text will be reset.

It is important to understand that the text on the LCD is cut to move the text that is outside of the LCD to the start of the LCD. This gives an effect that looks like the text moving from left to right. By printing the altered text every loop in the main.cpp the text moves from left to right. 

```cpp
void LCDScroll(){
    // Add one to the index to move the from left to right.
    placeIndex ++;
    // If the text reaches the end on the LCD reset the text.
    if (placeIndex > lcd_Chars){
        placeIndex = 0;
    }
    // Clear the LCD to place the new scroll text.
    lcd.clear();
    lcd.setCursor(0, 1);
    // Cut of text so it will not appear on the next line.
    int devideString = lcd_Chars - placeIndex;
    String tempdisplay_text = display_text.substring(0, devideString);
    String cutOffPartText = display_text.substring(devideString);
    String combinedCutText = cutOffPartText + "   " + tempdisplay_text;
    // Print the altered display text.
    lcd.print(combinedCutText);
}
```

### printLockerLCD function
The printLockerLCD function is called when a locker will be unlocked in the main.cpp file. The main.cpp file contains a if statemant that is allowed to pass when a user scans a valid card on our card reader. After the Wemos retrieves the locker that will be unlocked from the back-end API the locker number should be displayed by the LCD. This is done in the printLockerLCD function. The function reuires the locker number that will be unlocked. This locker number is stored in the main.cpp after using the api.cpp file to retrieve the correct locker number. This number is then send to the function as a function parameter. The retrieved number is stored as a String because the number is retrieved from the Json of the back-end API. The API echos the values as Strings. Now that the locker number is known the locker number can be displayed on the LCD screen. The printLockerLCD function differentiates the locker number being found or not. This is done because the locker sentence that will be used is not valid when no locker is found. After maing a no locker found sentence possible the temp_number variable can be simply added to a string and printed on the LCD screen. After the locker number is shown the scrolling text function will resume but the placeIndex variable will be reset to make sure the scroll function starts from scratch.

```cpp
void printLockerLCD(String temp_number){
    lcd.clear();
    if (temp_number == "No locker found."){
        lcd.print("No locker found.");
    }
    else {
        lcd.print("Locker " + temp_number + " unlocked.");
    }
    placeIndex = 0;
}
```

### LCD vendor
The LCD we are using was baught on Amazon. This is a link to the LCD screen found there: [LCD Screen](https://www.amazon.nl/dp/B0DFCH9V32?ref_=pe_28126711_487767311_302_E_DDE_dt_1).

### Libraries used
To make the code that was made for the LCD work the LiquidCrystal_I2C library was used. The library was added to the platformio.ini file. To look at the library I added a link to the library found online [LiquidCrystal_I2C library](https://www.arduinolibraries.info/libraries/liquid-crystal-i2-c). The LiquidCrystal_I2C library allows for our team to use functions to control  I2C displays. When using this library we can easily display text on our LCD.

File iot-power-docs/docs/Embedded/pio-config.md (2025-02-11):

# PlatformIO Configuration

This explains how to configure and use PlatformIO for multi-board compatibility, here for both the **D1 Mini Lite** (ESP8266) and the **ESP32 Devkit V1**.

The `platformio.ini` file defines environments for the D1 Mini Lite and ESP32 boards. Each environment includes board-specific settings, build flags, and library dependencies.

#### Configuration File:
```ini
[env:d1_mini_lite]
platform = espressif8266
board = d1_mini_lite
framework = arduino
build_flags = -DD1_MINI
lib_deps = 
    miguelbalboa/MFRC522@^1.4.11
    marcoschwartz/LiquidCrystal_I2C@^1.1.4
    bblanchon/ArduinoJson@^7.2.1

[env:esp32doit-devkit-v1]
platform = espressif32
board = esp32doit-devkit-v1
framework = arduino
monitor_speed = 115200
build_flags = -DESP_32
lib_deps = 
    miguelbalboa/MFRC522@^1.4.11
    marcoschwartz/LiquidCrystal_I2C@^1.1.4
    bblanchon/ArduinoJson@^7.2.1
```

The important thing here are the build flags, which are used to add specific macros according to the selected board :
  - `-DD1_MINI`: Defines `D1_MINI` for the ESP8266 environment.  
  - `-DESP_32`: Defines `ESP_32` for the ESP32 environment.  

---

### Example header for compatibility for both boards

This example header file provides board-specific includes and declarations, for connectivity functionality. 

```cpp
#ifndef EMBEDDED_CONNECTIVITY_H
#define EMBEDDED_CONNECTIVITY_H

#if defined(D1_MINI)
    #include <ESP8266WiFi.h>
    #include <ESP8266HTTPClient.h>
#elif defined(ESP_32)
    #include <WiFi.h>
    #include <HTTPClient.h>
#else
    #error "Please define a valid board (D1_MINI or ESP32)"
#endif

#include <WiFiClient.h>
#include <ArduinoJson.h>

void WiFiSetup();
String getLockerNumber();

#endif //EMBEDDED_CONNECTIVITY_H
```
---

To compile and upload the code for a specific board, select the appropriate environment in PlatformIO :
```bash
# Compile and upload for D1 Mini Lite
pio run --environment d1_mini_lite --target upload

# Compile and upload for ESP32 Devkit V1
pio run --environment esp32doit-devkit-v1 --target upload
```

### **Further references**
- PlatformIO documentation: [https://docs.platformio.org/](https://docs.platformio.org/)  
- Arduino reference: [https://www.arduino.cc/reference/en/](https://www.arduino.cc/reference/en/)  
- Libraries:  
  - [MFRC522](https://platformio.org/lib/show/161/MFRC522)  
  - [LiquidCrystal_I2C](https://platformio.org/lib/show/576/LiquidCrystal_I2C)  
  - [ArduinoJson](https://platformio.org/lib/show/64/ArduinoJson)

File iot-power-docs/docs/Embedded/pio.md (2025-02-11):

# PlatformIO

PlatformIO is a versatile development environment for embedded systems that supports a big range of boards and frameworks, including Arduino, ESP-IDF, and STM32.
Unlike the Arduino IDE, which is beginner-friendly but limited in features, PlatformIO offers advanced tools like dependency management, multiple environment configurations, and integration with IDEs like CLion, VSCode.
We use PlatformIO because it makes project organization easier, automates library handling, and provides a lot of debugging and testing capabilities, making it ideal for complex or multi-board projects.

### Prerequisites
1. An IDE installed on your machine.
2. **PlatformIO Core (CLI)** installed:
    - Follow the [PlatformIO installation guide](https://docs.platformio.org/en/latest/core/installation.html).

## PlatformIO projects structure

A typical PlatformIO project uses the following structure:

- **`src/`**: Contains the main source code files (`.cpp`).
    - Example: `src/main.cpp`
- **`include/`**: For additional header files (`.h`) used in the project.
- **`lib/`**: For custom libraries specific to a project.
- **`.pio/`**: PlatformIO’s build directory (generated after the first build). Not versioned in Git.
- **`test/`**: Contains unit tests.
- **`platformio.ini`**: Configuration file, described below

### `platformio.ini`
- This is the main configuration file for the project.
- Defines platforms, frameworks, libraries, and settings.
- Example:
  ```ini
  [env:esp32dev]
  platform = espressif32
  board = esp32dev
  framework = arduino
  lib_deps =
    adafruit/Adafruit BME280 Library
    arduino-libraries/WiFi
  ```

---

## Notes
- Ensure `platformio.ini` is properly configured for your board and environment. 
- Reload the project (Tools > PlatformIO > Reload in CLion) if your IDE does not recognize the PlatformIO project or doesn't detect libraries for example.
- Update the PlatformIO CLI regularly to ensure compatibility:
  ```bash
  pio upgrade
  ```

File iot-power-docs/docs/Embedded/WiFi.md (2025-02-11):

Our project requires the Wemos to fetch data from the back-end API. To do this a WiFi connection has to be made from the Wemos. After doing this the Wemos can use a web url to fetch Json data from the API. The WiFi connection is made in the wifi.cpp file of the project.

In the code snippet below it is shows that a WiFi connection can be made by using the WiFiClient.h and ArduinoJson.h libraries. The libraries make it possible to attempt a wifi connection using WiFi.begin with the given SSID and password. The while loop that checks WiFi.status() != WL_CONNECTED uses the WiFi status to determen wether a wifi connection is made 

The wifi setup fuction shown below tries to connect 4 times and then stops trying this is done so that the PlatformIO code does not stop working becuase of an infinite loop when the setup of the wifi is incorrect or the wifi is not available. For now the SSID and password are set to the Wemos that was used in Sam's personal project registered to the DLO because Sam made this code and used his own Wemos to test it.

```cpp
// Password and SSID for the Wifi.
#define WIFI_SSID "iotroam"
#define WIFI_PASSWORD "amqikyA95C"

// Set attempt variable to make sure the WiFi does not disrupt other functions when not able to connect.
int attemptCount = 0;

void WiFiSetup(){
    // Initialize the Serial-connection on a speed of 115200 b/s
    Serial.begin(115200);
    // Your WeMos tries to connect to your Wi-fi network  
    WiFi.begin(WIFI_SSID, WIFI_PASSWORD);
    // Keep the while-statement alive as long as we are NOT connected
    // to the Wi-fi network.
    while (WiFi.status() != WL_CONNECTED && attemptCount < 4) {
      delay(1000);
      Serial.println("Connecting to WiFi..");
      attemptCount ++;
    }
    Serial.println("Connected to the WiFi network");
}
```

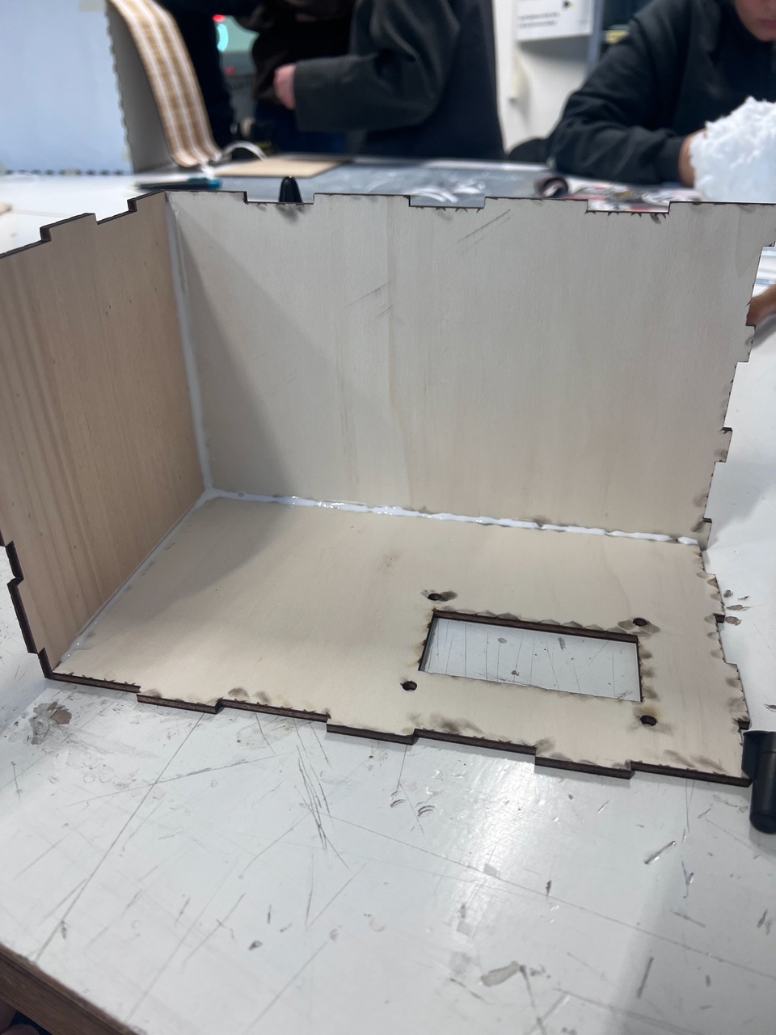
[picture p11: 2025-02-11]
design/casing3.jpg

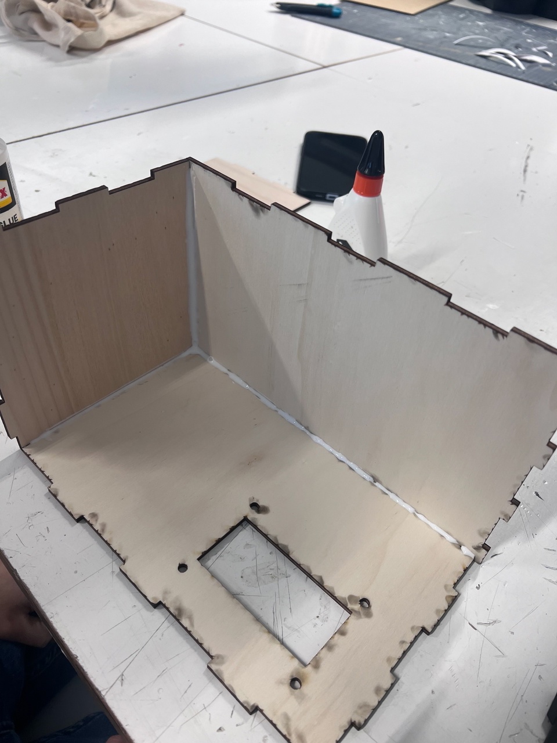
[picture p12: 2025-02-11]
design/casing.jpg

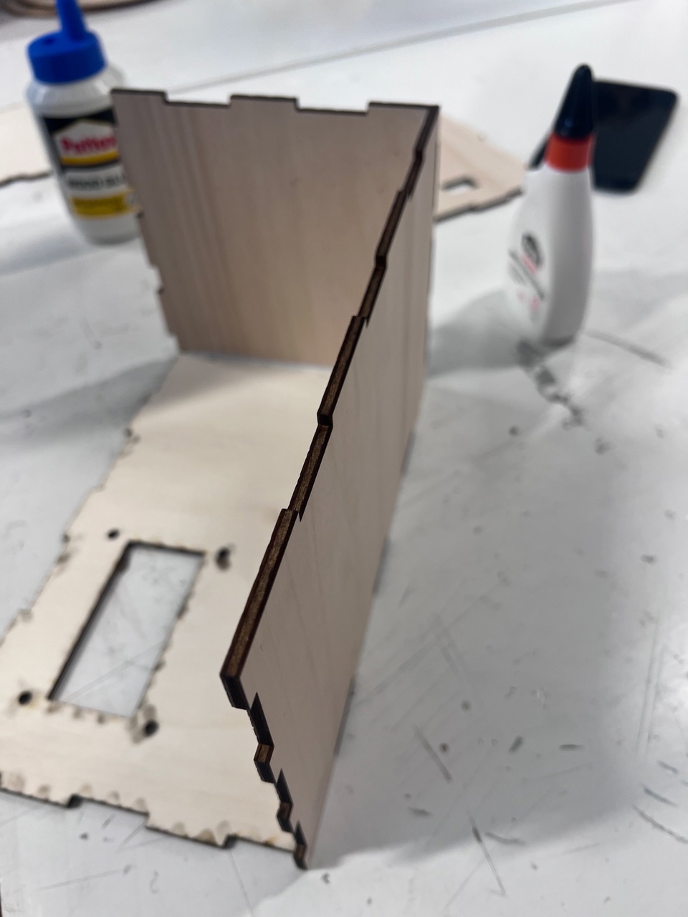
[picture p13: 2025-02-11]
design/casing2.jpg

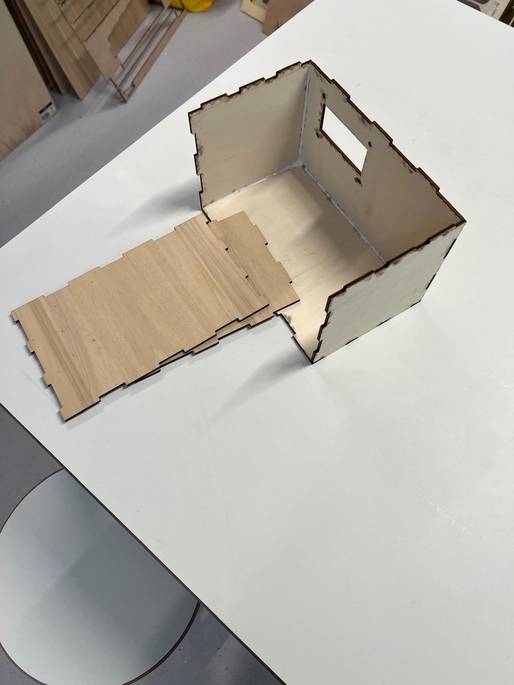
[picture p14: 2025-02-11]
design/casing4.jpg

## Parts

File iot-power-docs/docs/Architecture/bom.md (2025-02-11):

# Bill of Materials

This document serves as the Bill of Materials for this project. In here you can find a comprehensive list of parts and other materials needed for building this project.

## Table

| Part Number | Manufacturer | Description | Quantity | Price (excl VAT) EUR  | Price (incl VAT) EUR | Buy URL |
|---|---|---|---|---|---|---|
| WEMOS-D1-MINI-V4 | LOLIN | Wemos D1 Mini V4 - ESP8266 Microcontroller | 1 | €5.79 | €7.00 | [Link](https://www.tinytronics.nl/nl/development-boards/microcontroller-boards/met-wi-fi/wemos-d1-mini-v4-esp8266-ch340) |
| PN532MODKIT | NXP | RFID NFC Kit PN532 (with S50 Card and Key Tag) | 1 | €4.96 | €6.00 | [Link](https://www.tinytronics.nl/shop/nl/communicatie/rfid-nfc-kit-pn532-met-s50-kaart-en-s50-key-tag) |
| KY-003 | Unbranded | Hall Magnetic Sensor Module | 1 | €1.24 | €1.50 | [Link](https://www.tinytronics.nl/shop/product/hall-effect-switch-module) |
| B0DFCH9V32 | Binghe | LCD Display Module Binghe 2004 LCD Display 16x2 Characters Display Module I2C IIC Display 5V LCD with Backlight, Blue Screen, Compatible with Arduino with Raspberry Pi | 1 | €7.43 | €8.99 | [Link](https://www.amazon.nl/dp/B0DFCH9V32?ref_=pe_28126711_487767311_302_E_DDE_dt_1) |
| 10023001 | Alberts | Scharnier 80x80x1.25mm, RVS | 2 | €11.58 | €14.00 | [Link](https://www.praxis.nl/ijzerwaren/deurbeslag/deurscharnieren-paumelles/deurscharnieren/alberts-scharnier-verzonken-schroefgaten-rolbaar-vastgeklonken-rvs-pen-80x80x1-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) |
| - | Unbranded | Houtplaten 60x60x120cm | 2 | €7.44 | €9.00 | N/A |

**Total Cost (incl VAT): €37.50**

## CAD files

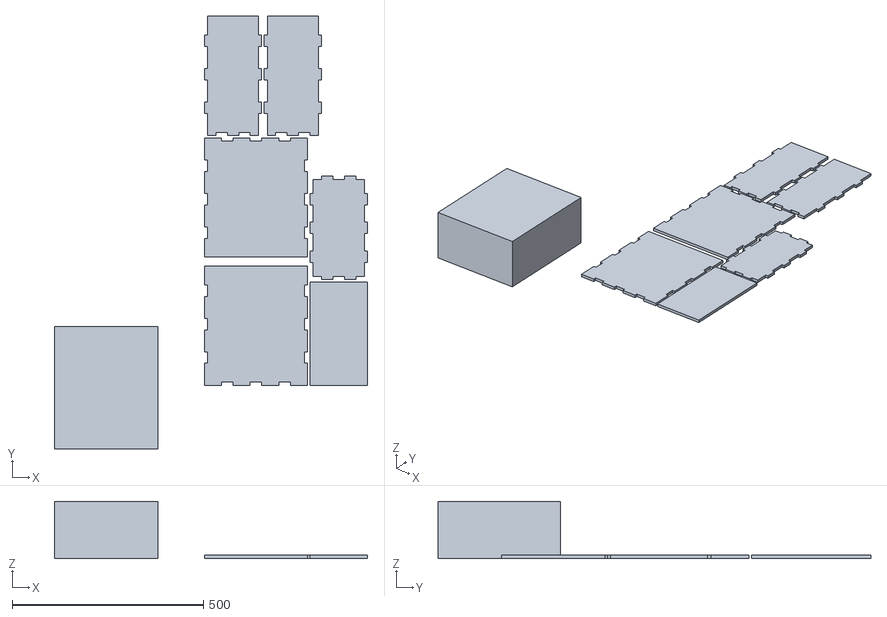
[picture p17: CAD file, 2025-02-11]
design/Locker_v2.stl
817.7 x 1130.9 x 150.0

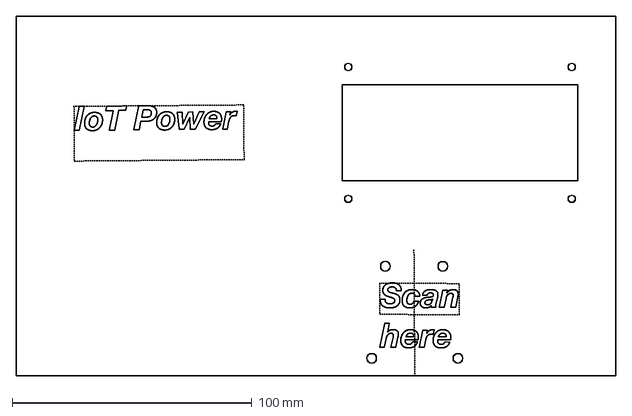
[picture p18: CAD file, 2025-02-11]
design/Dashboard_with_engraving.dxf
250.0 x 150.0 mm

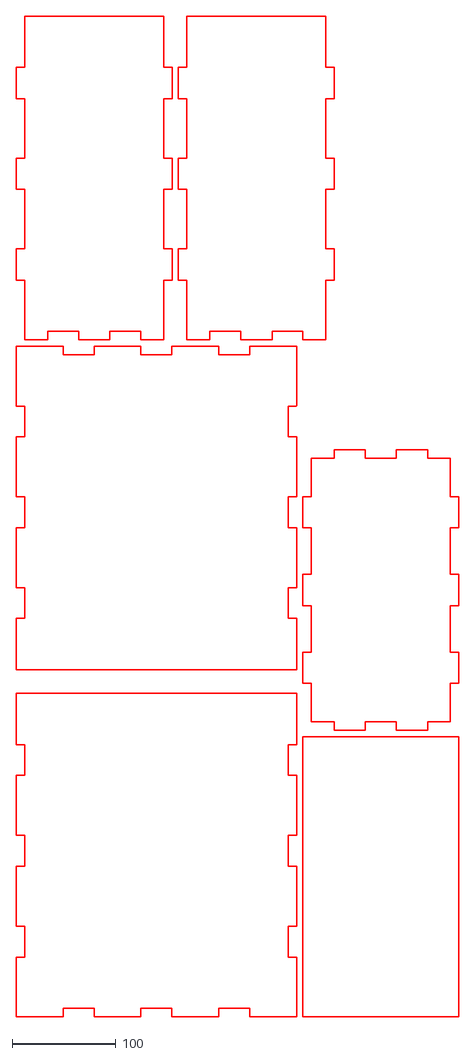
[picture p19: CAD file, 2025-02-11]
design/Prototype_box_v2.dxf
426.5 x 964.7

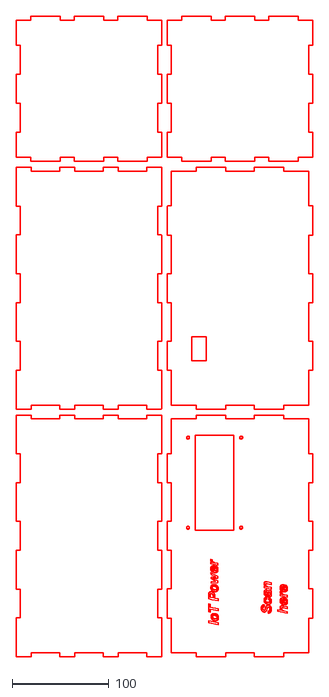
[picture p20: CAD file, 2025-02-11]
design/2d_render_dashboard.dxf
306.5 x 662.8

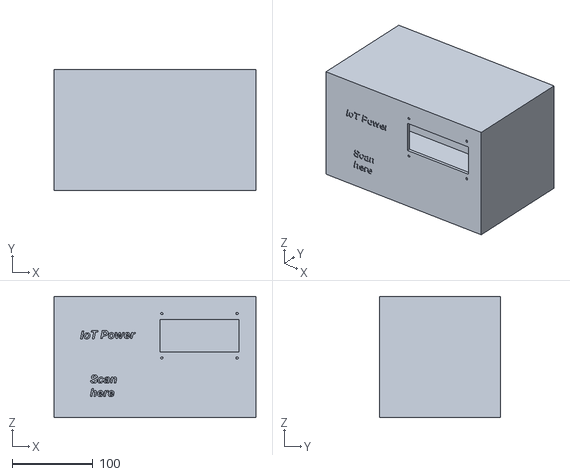
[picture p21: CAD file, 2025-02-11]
design/New_dashboard_casing.stl
250.0 x 150.0 x 150.0

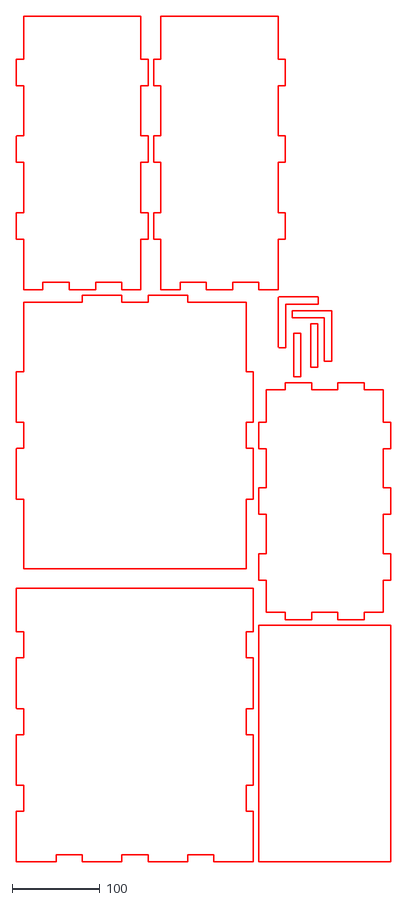
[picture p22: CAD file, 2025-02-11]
design/Prototype_box_v2_outer.dxf
426.5 x 964.7

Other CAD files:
design/Box for embedded device.f3z
design/Dashboard.f3z
design/Dashboard_v2.f3d
design/Locker.blend
design/Locker_v2.f3d
design/New_dashboard_casing.f3d
design/Prototype_box_v2_outer.dwg
design/locker-rack.blend
iot-power-docs/static/design/LockerDesignV1.f3d

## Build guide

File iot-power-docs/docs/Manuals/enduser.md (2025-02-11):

# IoT Power - End User Manual

## How to Use the Locker System

1. Approach the IoT Power locker system.
2. Locate the card reader on the locker panel.
3. Have your student card ready.

### Borrowing a Power Reel

1. Tap your student card on the card reader.
2. Wait for the system to process your request.
3. When approved, the LCD screen will display an available locker number (e.g., "Locker 5 Open").
4. Open the assigned locker and remove the power reel.
5. Close the locker door securely.

### Returning a Power Reel

1. Approach any available locker with your borrowed power reel.
2. Tap your student card on the card reader.
3. Wait for the system to process your return.
4. When approved, a locker will open automatically.
5. Place the power reel inside the open locker.
6. Close the locker door securely.

## Using the QR Code

1. Locate the QR code displayed on the locker system or in designated areas around campus.
2. Open the camera app on your smartphone.
3. Point your camera at the QR code.
4. Tap on the notification that appears to open the link.

# User Manual: IoT Power Locker System

## How to Use the Locker System

1. Approach the IoT Power locker system.
2. Locate the QR code displayed on the locker or nearby signage.
3. Use your smartphone to scan the QR code. This will redirect you to our website.
4. On the website, follow the instructions to authenticate using your student credentials.
5. Once authenticated, you will receive a locker number on your phone.
6. Go to the assigned locker number.
7. Use your student card to unlock the locker by tapping it on the card reader.
8. The locker will open, allowing you to retrieve or return a power reel.
9. After taking or returning a power reel, close the locker door securely.
10. The system will automatically record your transaction.

## Returning Power Reels

1. When you're done using the power reel, return to any available locker.
2. Scan the QR code again and authenticate on the website.
3. You'll be assigned an available locker for return.
4. Use your student card to open the assigned locker.
5. Place the power reel inside.
6. Close the locker door securely.

## Tips

- Always handle the power reels with care.
- Report any issues or damaged equipment to the faculty staff immediately.
- Ensure you return the power reel within the designated borrowing period to avoid any penalties.

For more information or assistance, please contact the HBO-ICT faculty support desk.

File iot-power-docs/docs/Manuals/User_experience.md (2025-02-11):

# User Experience Flow for the Embedded Locker System

## Overview
The embedded locker system integrates various IoT components such as an RFID card reader, LCD screen, Hall sensor, buzzer, and connectivity modules to provide a seamless and interactive user experience. The system allows users to borrow or return power cables by interacting with lockers.

---
## User Interaction Flow

### 1. **Initialization**
   - **System Boot**:
     - When powered on, the system initializes its components, including the Hall sensor, LCD, buzzer, and connectivity modules.
     - The LCD screen displays a welcome message: `"Please scan card."`

### 2. **RFID Card Interaction**
   - **Card Scan**:
     - The user scans their RFID card at the reader.
     - The buzzer beeps briefly to confirm a successful scan.
     - **If Card is Invalid**:
       - The LCD displays: `"Please register your card."`
       - The system halts further actions until a valid card is scanned.
   - **Backend Validation**:
     - The system communicates with the backend API to authenticate the card and retrieve the user’s details.
     - **Error Handling**:
       - If the user is not found, an error message is displayed on the LCD.

### 3. **Locker Availability Check**
   - **Using the Hall Sensor**:
     - The Hall sensor detects whether a locker is occupied or available by measuring magnetic fields.
     - If the locker is occupied, the LCD shows: `"No power reel available."`
     - If available, the system proceeds to assign a locker.

### 4. **Locker Assignment and Unlocking**
   - **Assigning a Locker**:
     - The system assigns a locker based on user requirements (e.g., borrowing or returning).
     - The assigned locker number is displayed on the LCD: `"Locker X unlocked."`
     - The locker’s LED indicator blinks to help the user locate it.
   - **Unlocking**:
     - The locker is unlocked, and the buzzer activates briefly as a confirmation signal.

### 5. **User Interaction with the Locker**
   - **Borrowing a Cable**:
     - The LCD prompts: `"Please take the power cable from locker X."`
     - The Hall sensor verifies that the cable has been removed.
     - If the locker door is closed without removing the cable, the LCD shows: `"Transaction aborted."` and logs the error.
   - **Returning a Cable**:
     - The LCD prompts: `"Please place the power cable in locker X."`
     - The Hall sensor confirms that the cable has been replaced.
     - If the locker door is closed without replacing the cable, the LCD shows: `"Transaction aborted."` and logs the error.

### 6. **Transaction Completion**
   - **Final Steps**:
     - Once the user completes their action (borrowing or returning), the LCD prompts: `"Please close the door of locker X."`
     - The system waits for the locker door to be securely closed.
     - A thank-you message is displayed: `"Thank you for using the IoT Power cable station."`
   - **Reset**:
     - The system resets to the idle state, ready for the next user.

---

## Feedback Mechanisms

### Visual Feedback
   - **LCD Screen**:
     - Displays real-time messages and instructions, such as "Locker unlocked," "Please scan card," and error messages.
     - Scrolls text for longer messages to ensure readability.
   - **LED Indicators**:
     - Blink to guide the user to the correct locker during a transaction.

### Audio Feedback
   - **Buzzer**:
     - Activates briefly to confirm actions such as card scans and locker unlocks.

### Sensor Feedback
   - **Hall Sensor**:
     - Monitors the presence of magnetic fields to determine locker occupancy and track user actions.

---
# User Experience Flow for the Embedded Locker System

## Overview
The embedded locker system integrates various IoT components such as an RFID card reader, LCD screen, Hall sensor, buzzer, and connectivity modules to provide a seamless and interactive user experience. The system allows users to borrow or return power cables by interacting with lockers.

---

## User Interaction Flow

### 1. **Initialization**
   - **System Boot**:
     - When powered on, the system initializes its components, including the Hall sensor, LCD, buzzer, and connectivity modules.
     - The LCD screen displays a welcome message: `"Please scan card."`

### 2. **RFID Card Interaction**
   - **Card Scan**:
     - The user scans their RFID card at the reader.
     - The buzzer beeps briefly to confirm a successful scan.
     - **If Card is Invalid**:
       - The LCD displays: `"Please register your card."`
       - The system halts further actions until a valid card is scanned.
   - **Backend Validation**:
     - The system communicates with the backend API to authenticate the card and retrieve the user’s details.
     - **Error Handling**:
       - If the user is not found, an error message is displayed on the LCD.

### 3. **Locker Availability Check**
   - **Using the Hall Sensor**:
     - The Hall sensor detects whether a locker is occupied or available by measuring magnetic fields.
     - If the locker is occupied, the LCD shows: `"No power reel available."`
     - If available, the system proceeds to assign a locker.

### 4. **Locker Assignment and Unlocking**
   - **Assigning a Locker**:
     - The system assigns a locker based on user requirements (e.g., borrowing or returning).
     - The assigned locker number is displayed on the LCD: `"Locker X unlocked."`
     - The locker’s LED indicator blinks to help the user locate it.
   - **Unlocking**:
     - The locker is unlocked, and the buzzer activates briefly as a confirmation signal.

### 5. **User Interaction with the Locker**
   - **Borrowing a Cable**:
     - The LCD prompts: `"Please take the power cable from locker X."`
     - The Hall sensor verifies that the cable has been removed.
     - If the locker door is closed without removing the cable, the LCD shows: `"Transaction aborted."` and logs the error.
   - **Returning a Cable**:
     - The LCD prompts: `"Please place the power cable in locker X."`
     - The Hall sensor confirms that the cable has been replaced.
     - If the locker door is closed without replacing the cable, the LCD shows: `"Transaction aborted."` and logs the error.

### 6. **Transaction Completion**
   - **Final Steps**:
     - Once the user completes their action (borrowing or returning), the LCD prompts: `"Please close the door of locker X."`
     - The system waits for the locker door to be securely closed.
     - A thank-you message is displayed: `"Thank you for using the IoT Power cable station."`
   - **Reset**:
     - The system resets to the idle state, ready for the next user.

---

## Feedback Mechanisms

### Visual Feedback
   - **LCD Screen**:
     - Displays real-time messages and instructions, such as "Locker unlocked," "Please scan card," and error messages.
     - Scrolls text for longer messages to ensure readability.
   - **LED Indicators**:
     - Blink to guide the user to the correct locker during a transaction.

### Audio Feedback
   - **Buzzer**:
     - Activates briefly to confirm actions such as card scans and locker unlocks.

### Sensor Feedback
   - **Hall Sensor**:
     - Monitors the presence of magnetic fields to determine locker occupancy and track user actions.

---

## System Reliability

### Offline Mode
   - If WiFi connectivity is lost, the system operates in offline mode using local storage to manage basic transactions.

### Error Logging
   - Logs all errors, such as invalid card scans or failed transactions, for troubleshooting and diagnostics.

---

## Conclusion
The embedded locker system prioritizes a smooth and intuitive user experience by combining hardware components like LCDs, buzzers, and sensors with robust software logic. By providing clear instructions, real-time feedback, and reliable functionality, it ensures that users can borrow or return power cables with ease.

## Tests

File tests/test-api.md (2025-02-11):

# Project Setup and Test Script Execution

## Steps to Run the Test Script

### 1. Start the Containers

In the root directory of your project, start the Docker containers using Docker Compose.

```bash
docker-compose -f docker-compose-test.yml up -d --force-recreate --build
```
This command will start all the services defined in the docker-compose.yml file in detached mode (-d), meaning the containers will run in the background.

### 2. Run the test script

```bash
bash test-api.sh
```

## What the Script Does

The script does the following:

- Verify if the getAvailableLocker function is working.
- Verify if the getCables function is working.
- Verify if the getUser function is working.
- Verify if the getUser function is working with misformed user ID's
- Verify if the getUser function is working with nonexistent user ID's
- Verify if the getUser function is working with no user ID parameter

It will also stress test every function.

If all tests pass, the script will output:

```
echo "All API calls verified successfully."
```

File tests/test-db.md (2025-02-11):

# Project Setup and Test Script Execution

## Steps to Run the Test Script

### 1. Start the Containers

In the root directory of your project, start the Docker containers using Docker Compose.

```bash
docker-compose -f docker-compose-test.yml up -d --force-recreate --build
```
This command will start all the services defined in the docker-compose.yml file in detached mode (-d), meaning the containers will run in the background.

### 2. Run the test script

```bash
bash test-db.sh
```

## What the Script Does

The script does the following:

- Verify if the MariaDB container is working.
- Verify if the locker database exists
- Verify if the 'Cable' table exists
- Verify if the 'Locker' table exists
- Verify if the 'User' table exists

If all tests pass, the script will output:

```
echo "Database and tables verified successfully"
```

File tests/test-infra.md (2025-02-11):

# Project Setup and Test Script Execution

## Steps to Run the Test Script

### 1. Start the Containers

In the root directory of your project, start the Docker containers using Docker Compose.

```bash
docker-compose -f docker-compose-test.yml up -d --force-recreate --build
```
This command will start all the services defined in the docker-compose.yml file in detached mode (-d), meaning the containers will run in the background.

### 2. Run the test script

```bash
sh test-infra.sh
```

## What the Script Does

The script performs several checks to ensure the following services are available:

- Nginx Server: The script checks if the Nginx container is accessible.
- phpMyAdmin: The script checks if phpMyAdmin works.
- API Endpoint: The script checks if the API is working.
- MariaDB: The script checks if the MariaDB container is working.

If all tests pass, the script will output:

```
Tests ran successfully
```

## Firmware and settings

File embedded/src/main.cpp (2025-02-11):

#include "cardManager.h"
#include "LCD.h"
#include "hall-sensor.h"


#if ONLINE_MODE
#include "connectivity.h"
#include "api.h"
#include "buzzer.h"
#include "locker.h"
#else
#include "locker_offline.h"
#endif

// Variable hold the scanned card uid.
String uid = "";
// Define the amount of lcd characters.
int lcd_Chars_Amount = 20;

const int buzzerPin = 6;
unsigned long currentMillis = 0;

unsigned long cardScanInterval = 5000;
unsigned long lcdScrollInterval = 500;
unsigned long wifiHealthCheckInterval = 300000; // 5 minutes

unsigned long previousCardScanMillis = 0;
unsigned long previousLcdScrollMillis = 0;
unsigned long previousWifiCheckMillis = 0;

void setup() {
    Serial.begin(9600);   // Initiate a serial communication
    cardManagerSetup();
    LCDSetup();

    setupHallSensor();

    #if ONLINE_MODE
    WiFiSetup();
    buzzerSetup();
    #endif
    
    Serial.println("All lockers initialized and locked.");
}


void loop() {

    // Simulate locker operations
    #if LOCKER_MECHANISM_TEST
    for (int i = 0; i < numLockers; i++) {
        // Unlock a locker
        unlockLocker(i);
        delay(5000); // Keep it unlocked for 5 seconds
    }
    #endif

    currentMillis = millis(); // Overflows in 49.67 days, fix later

    if (currentMillis - previousLcdScrollMillis >= lcdScrollInterval) {
        previousLcdScrollMillis = currentMillis;  // Update the last LCD scroll time
        LCDScroll();
    }

    if (currentMillis - previousCardScanMillis >= cardScanInterval) {
        previousCardScanMillis = currentMillis;  // Update the last card scan time
        uid = readCard();
        #if ONLINE_MODE
            if (uid != "") {
                String userId = getUserIdWithUID(uid); // Get the user ID from the database based on the uid from the card reader.
                if (userId == "No user found."){
                    displayMessage("Please register your card.", 5000);
                } else {
                    String reservation = checkForReservation(userId);
                    if (reservation == "None"){
                        String availableLocker = getLockerNumberWithTransaction(userId); // Get the unlocked locker number using the user ID
                        String transactionType = getTransactionType(userId); // Get the transaction type from the user ID
                        printInteractionLCD(availableLocker, transactionType, userId); // Print all steps the user has to do to complete their transaction
                    } else {
                        String availableLocker = retrieveReservation(reservation); // Get the unlocked locker number using the reservation ID.
                        // Get all the lockerIds in case multiple lockers where reserved.
                        String availableLockerArray[25];
                        int index = 0;
                        int startIndex = 0;
                        int commaIndex = availableLocker.indexOf(',');
                        // Seperate the reservation string by comma.
                        while (commaIndex != -1) {
                            availableLockerArray[index] = availableLocker.substring(startIndex, commaIndex);
                            index++;
                            startIndex = commaIndex + 1;
                            commaIndex = availableLocker.indexOf(',', startIndex);
                        }
                        // Add the last substring after the last comma.
                        availableLockerArray[index] = availableLocker.substring(startIndex);
                        // Call printInteractionLCD function for every reservation made.
                        for (int i = 0; i <= index; i++) {
                            printInteractionLCD(availableLockerArray[i], "Lending", userId); // Print all steps the user has to do to complete their transaction.
                        }
                    }
                }
            }
        #else
            if (uid != "") {
                determineTransaction(uid);
            }
        #endif
    }

    #if ONLINE_MODE
        if (currentMillis - previousWifiCheckMillis >= wifiHealthCheckInterval) {
            previousWifiCheckMillis = currentMillis;  // Update the last Wi-Fi health check time
            if (WiFi.status() != WL_CONNECTED) {
                Serial.println("Wi-Fi connection lost. Reconnecting...");
                WiFiSetup();
            } else {
                Serial.println("Wi-Fi is connected.");
            }
        }
    #endif
}

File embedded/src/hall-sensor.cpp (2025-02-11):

#include "hall-sensor.h"

// Initialize the Hall Sensor
void setupHallSensor() {
    Serial.println("Initializing Hall Sensor...");
    pinMode(HALL_SENSOR_PIN, INPUT);
    Serial.println("Hall Sensor initialized.");
}

// Check locker availability based on Hall Sensor readings
void checkLockerAvailability() {
    Serial.println("Checking locker availability using Hall Sensor...");
    int sensorValue = analogRead(HALL_SENSOR_PIN);
    Serial.print("Sensor Value: ");
    Serial.println(sensorValue);

    if (sensorValue > MAGNET_DETECTED_THRESHOLD) {
        Serial.println("Magnetic field detected: Locker is occupied.");
    } else {
        Serial.println("No magnetic field detected: Locker is available.");
    }
}
